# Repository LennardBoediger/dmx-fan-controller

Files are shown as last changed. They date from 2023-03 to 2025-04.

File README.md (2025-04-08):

# DMX Fan Controller
Speed controller for two old industrial fans.

https://user-images.githubusercontent.com/11893651/213900107-9a194785-94d3-4e1d-9f15-b6ec5db4715c.mov

<br>
The final installation will use two fans, a powerful fog machine and a stroboscope to create a neat effect.<br>

## Documentation 
The Fans are powerd by three-phase alternating current and come with an 0-10V control line. The lowest possible speed setting during runtime is 1.6V but 2.6V is required to start the motors from standstill

The controller board is based on the Arduino Nano (ATmega328).<br>
For the Fan Control line a 0-5V 10Bit DAC is used. The output voltage is then amplified, so that we end up with an 0-10V 10Bit DAC.<br>
To communicate over the DMX-Bus, the board is equipped with an MAX485E RS-485 transceiver.<br>
The DMX channel can be selected using a DIP switch.<br>
Additionally there is an manual control override, which allows the fan to be set to a constant speed.<br>
Mounting holes are M3.
#### Schematic:
Schematic-v2

## Safety instructions
Please don't die when using large spinning fan blades that are powered by three-phase current.

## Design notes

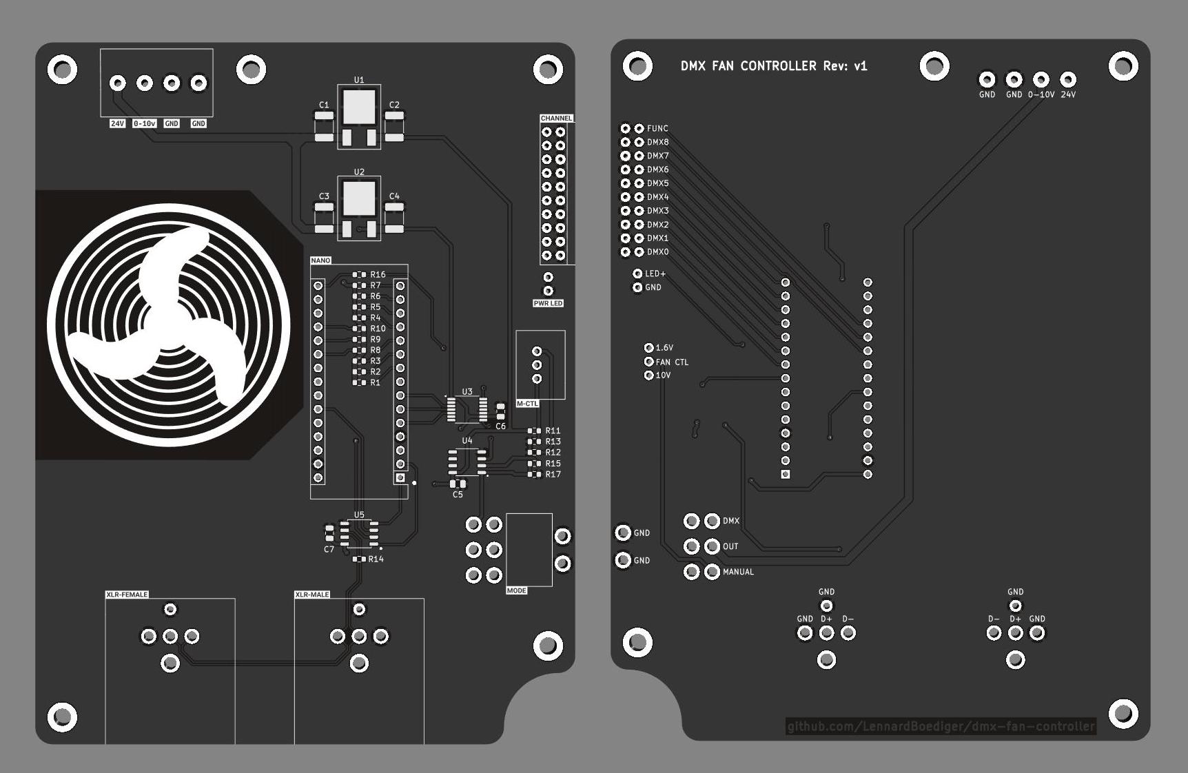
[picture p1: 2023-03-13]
.img/fan-controller-pcb-rendering.jpg

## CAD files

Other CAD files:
hardware/fan-controller-pcb/edge_cuts.FCStd

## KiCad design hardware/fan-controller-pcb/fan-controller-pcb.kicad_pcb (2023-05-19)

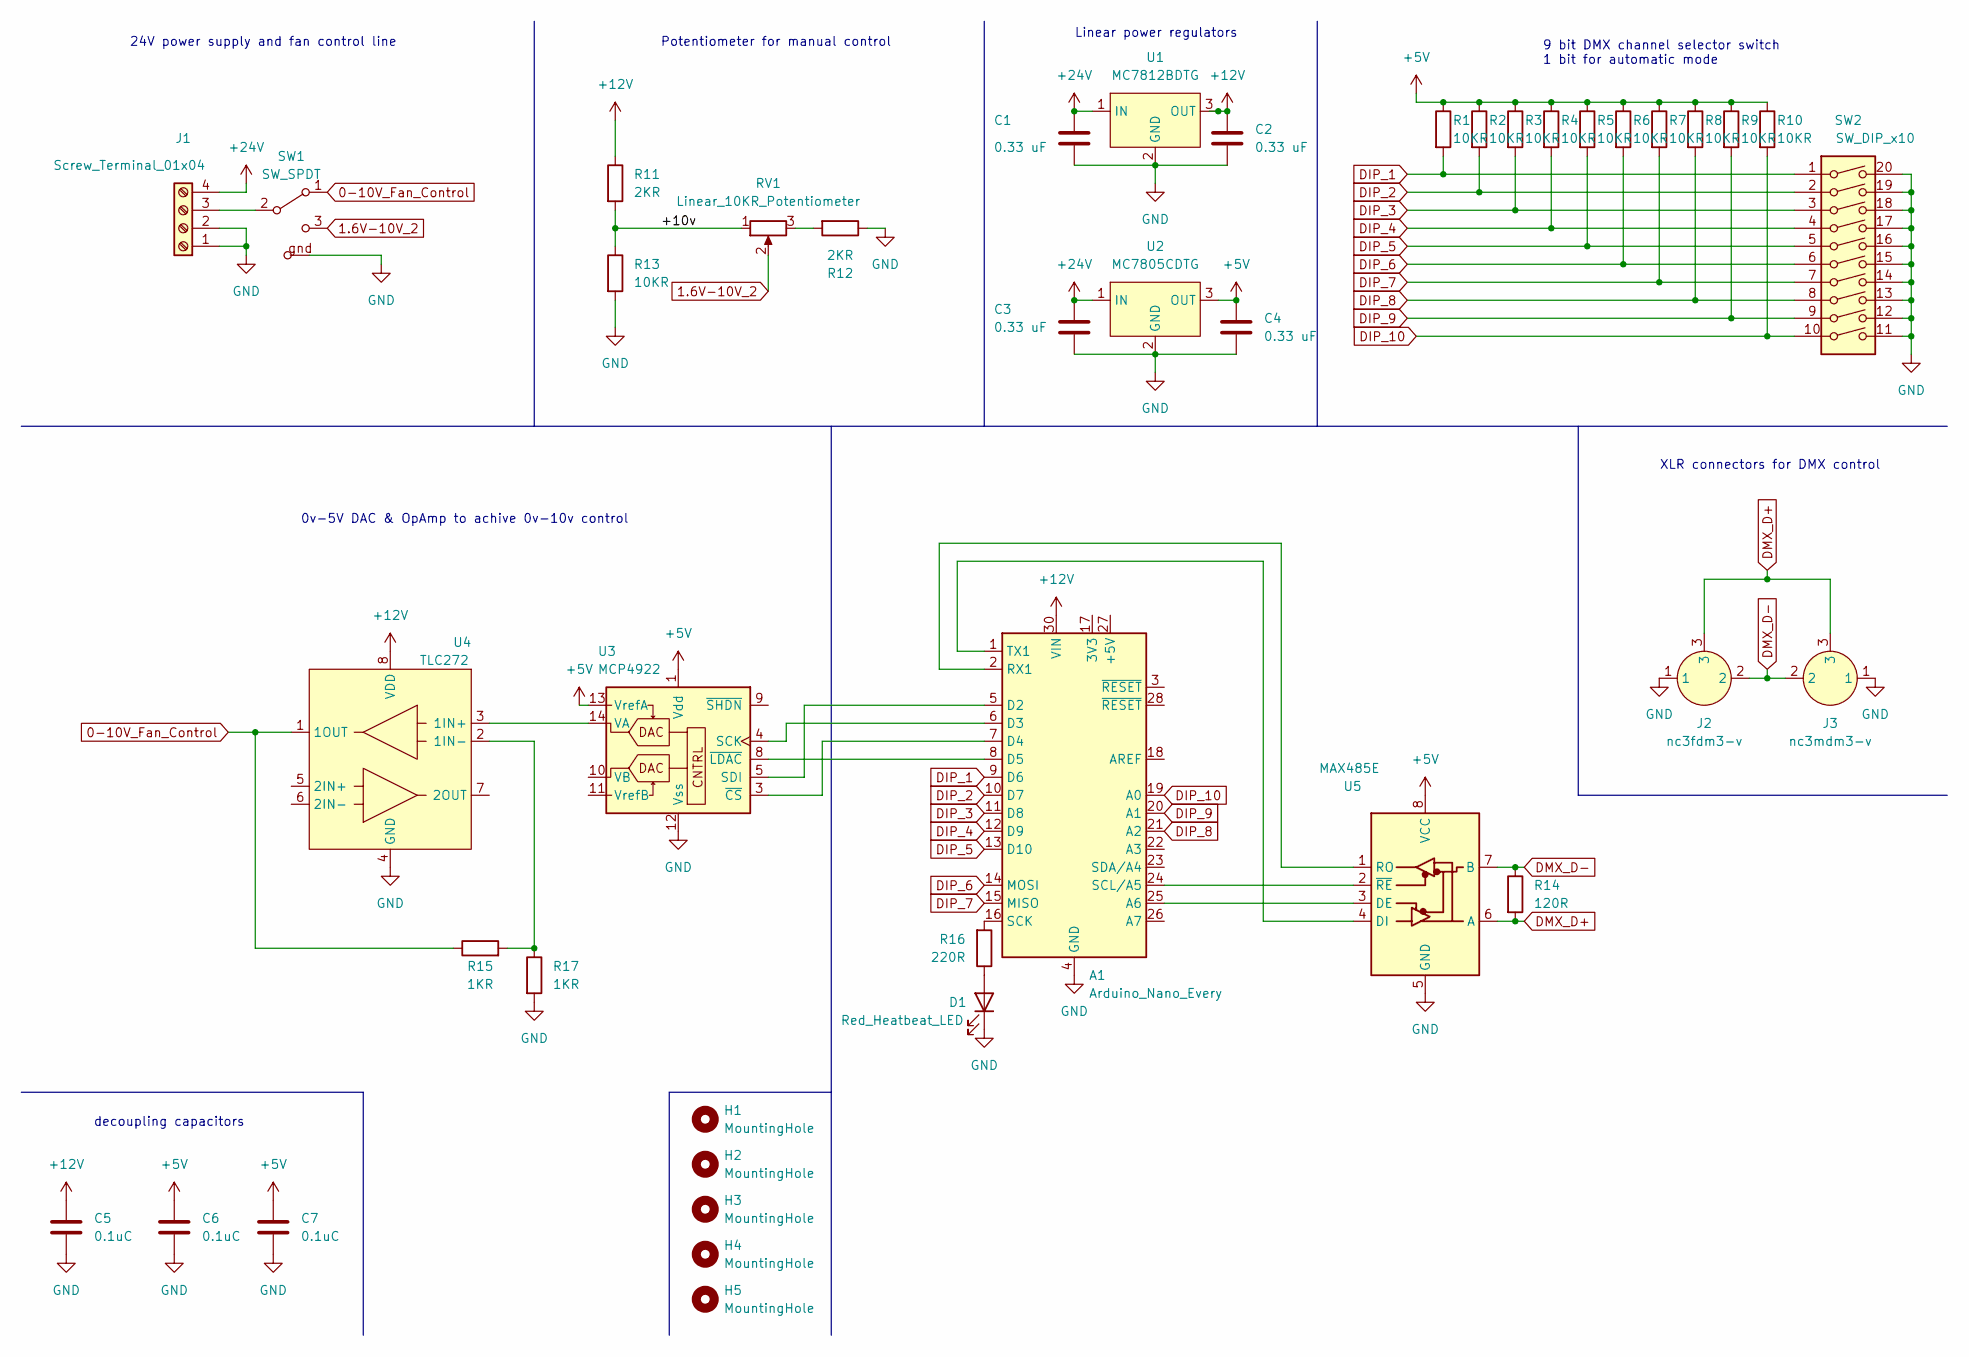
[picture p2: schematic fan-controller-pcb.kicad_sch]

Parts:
A1: Arduino_Nano_Every; Arduino_Nano
C1, C2, C3, C4: 0.33 uF; C_1812_4532Metric
C5, C6, C7: 0.1uC; C_0805_2012Metric
D1: Red_Heatbeat_LED; LED_D3.0mm_Horizontal_O1.27mm_Z6.0mm
H1, H2, H3, H4, H5: MountingHole; MountingHole_3.2mm_M3_ISO14580_Pad_TopBottom
J1: Screw_Terminal_01x04; TerminalBlock_Altech_AK300-4_P5.00mm
J2: nc3fdm3-v; nc3fdm3-h
J3: nc3mdm3-v; nc3mdm3-h
R1, R2, R3, R4, R5, R6, R7, R8, R9, R10, R13: 10KR; R_0603_1608Metric
R11, R12: 2KR; R_0603_1608Metric
R14: 120R; R_0603_1608Metric
R15, R17: 1KR; R_0603_1608Metric
R16: 220R; R_0603_1608Metric
RV1: Linear_10KR_Potentiometer; Potentiometer_Vishay_148-149_Single_Horizontal
SW1: SW_SPDT; WS-TOTV_6.35_Right_Angle_Toggle_Switch
SW2: SW_DIP_x10; WS-DITU_Compact_THT_Right_Angled
U1: MC7812BDTG
U2: MC7805CDTG; MC785BDTG
U3: MCP4922; MCP4912
U4: TLC272; tlc272a
U5: MAX485E

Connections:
0-10V_Fan_Control: R15.1, SW1.1 (A), U4.1 (1OUT)
1.6V-10V_2: RV1.2, SW1.3 (C)
+5V: C4.1, C6.1, C7.1, R1.1, R2.1, R3.1, R4.1, R5.1, R6.1, R7.1, R8.1, R9.1, R10.1, U2.3 (OUT), U3.1 (Vdd), U3.13 (VrefA), U5.8 (VCC)
+12V: A1.30 (VIN), C2.1, C5.1, R11.1, U1.3 (OUT), U4.8 (VDD)
+24V: C1.1, C3.1, J1.4, U1.1 (IN), U2.1 (IN)
/+10v: R11.2, R13.1, RV1.1
DIP_1: A1.9 (D6), R1.2, SW2.1
DIP_2: A1.10 (D7), R2.2, SW2.2
DIP_3: A1.11 (D8), R3.2, SW2.3
DIP_4: A1.12 (D9), R4.2, SW2.4
DIP_5: A1.13 (D10), R5.2, SW2.5
DIP_6: A1.14 (MOSI), R6.2, SW2.6
DIP_7: A1.15 (MISO), R7.2, SW2.7
DIP_8: A1.21 (A2), R8.2, SW2.8
DIP_9: A1.20 (A1), R9.2, SW2.9
DIP_10: A1.19 (A0), R10.2, SW2.10
DMX_D+: J2.3, J3.3, R14.2, U5.6 (A)
DMX_D-: J2.2, J3.2, R14.1, U5.7 (B)
GND: A1.4 (GND), A1.29 (GND), C1.2, C2.2, C3.2, C4.2, C5.2, C6.2, C7.2, D1.1 (K), J1.1, J1.2, J2.1, J3.1, R12.1, R13.2, R17.2, SW1.gnd (GND), SW2.11, SW2.12, SW2.13, SW2.14, SW2.15, SW2.16, SW2.17, SW2.18, SW2.19, SW2.20, U1.2 (GND), U2.2 (GND), U3.12 (Vss), U4.4 (GND), U5.5 (GND)
unnamed: A1.1 (TX1), U5.4 (DI)
unnamed: A1.2 (RX1), U5.1 (RO)
unnamed: A1.5 (D2), U3.5 (SDI)
unnamed: A1.6 (D3), U3.4 (SCK)
unnamed: A1.7 (D4), U3.3 (~CS)
unnamed: A1.16 (SCK), R16.2
unnamed: A1.24 (SCL/A5), U5.2 (~RE)
unnamed: A1.25 (A6), U5.3 (DE)
unnamed: D1.2 (A), R16.1
unnamed: J1.3, SW1.2 (B)
unnamed: R12.2, RV1.3
unnamed: R15.2, R17.1, U4.2 (1IN-)
unnamed: U3.14 (VA), U4.3 (1IN+)

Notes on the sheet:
24V power supply and fan control line
Potentiometer for manual control
0v-5V DAC & OpAmp to achive 0v-10v control
Linear power regulators
XLR connectors for DMX control
9 bit DMX channel selector switch 1 bit for automatic mode
decoupling capacitors

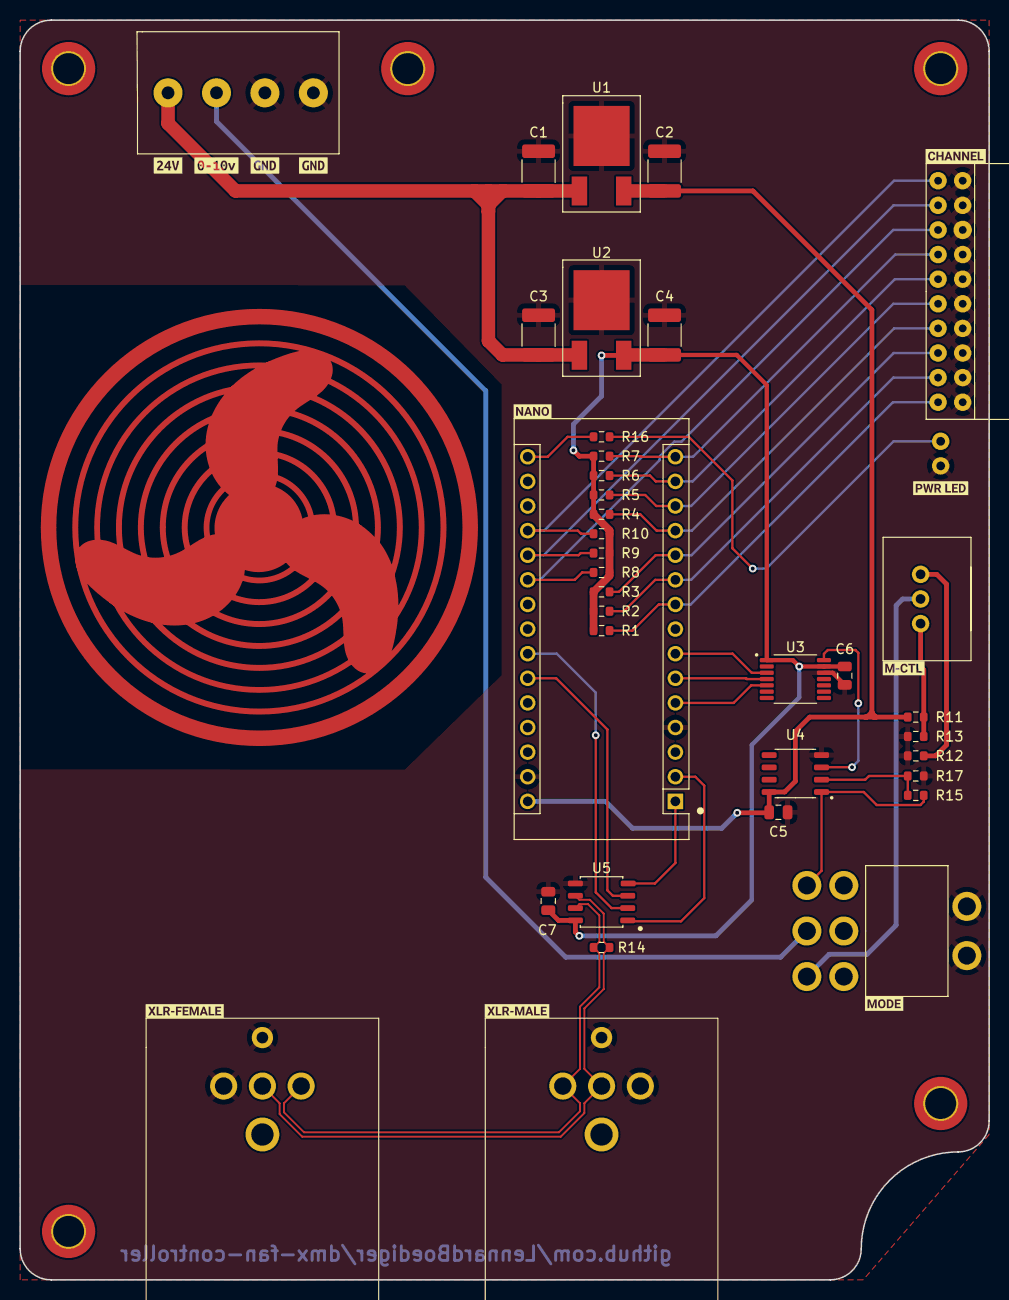
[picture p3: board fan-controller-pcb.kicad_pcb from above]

Board: 2 copper layers, 100.0 x 130.0 mm, 53 parts (0 on the bottom side), 32 nets.

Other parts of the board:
kibuzzard-63FA74A1: G***; kibuzzard-63FA74A1
kibuzzard-63FA74BB: G***; kibuzzard-63FA74BB
kibuzzard-63FA74F3: G***; kibuzzard-63FA74F3
kibuzzard-63FA7528: G***; kibuzzard-63FA7528
kibuzzard-640DCC4D: G***; kibuzzard-640DCC4D
kibuzzard-640DCC6D: G***; kibuzzard-640DCC6D
kibuzzard-640DCC52: G***; kibuzzard-640DCC52
kibuzzard-640DCC68: G***; kibuzzard-640DCC68
kibuzzard-640DCC72: G***; kibuzzard-640DCC72
kibuzzard-640DCC79: G***; kibuzzard-640DCC79
kibuzzard-640DCC82: G***; kibuzzard-640DCC82

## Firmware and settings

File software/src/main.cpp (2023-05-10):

#include <Arduino.h>
#include <DMXSerial.h>

#define DAC_MAX_VALUE 4095
#define DAC_MIN_VALUE 0
#define DMX_MAX_VALUE 255

// SPI Pins for DAC
const int CSPin = 4;
const int SCKPin = 3;
const int MOSIPin = 2;

// DIP switch pins for DMX address 
const int DMX0 = 6;
const int DMX1 = 7;
const int DMX2 = 8;
const int DMX3 = 9;
const int DMX4 = 10;
const int DMX5 = 11;
const int DMX6 = 12;
const int DMX7 = 16;
const int DMX8 = 15;
const int DMXfunc = 14;

// This function transmits data via SPI to the DAC (MCP4922)
// WRITE COMMAND REGISTER FOR MCP4922 (12-BIT DAC):
// Bit 15: channel (A=0, B=1), 
// Bit 14: Buffer (default=0), 
// Bit 13: Gain (1x=1, 2x=0), 
// Bit 12: shutdown (active=1. inactive-0),
// Bit 11-0: DAC Input Data bits.
// p. 24
void setDac(unsigned long value){ 
  unsigned long dacRegister = 0b0011000000000000;
  // Set channel A
  dacRegister &= ~(1 << 15);
  // Generate the two bytes that will be sent to the DAC
  unsigned long dacSendBytes = dacRegister | value;

  // Start SPI transmission
  digitalWrite(CSPin, LOW); 
  for(int i = 0; i < 16; i++){
    digitalWrite(MOSIPin, bitRead(dacSendBytes, 15-i));
    delay(2);
    digitalWrite(SCKPin, HIGH);
    delay(2);
    digitalWrite(SCKPin, LOW);
  }
  digitalWrite(CSPin, HIGH);
}

void setup() {
  // SPI
  pinMode(CSPin, OUTPUT);
  pinMode(SCKPin, OUTPUT);
  pinMode(MOSIPin, OUTPUT);
  digitalWrite(CSPin, HIGH);
  //DMX
  pinMode(DMX0, INPUT);
  pinMode(DMX1, INPUT);
  pinMode(DMX2, INPUT);
  pinMode(DMX3, INPUT);
  pinMode(DMX4, INPUT);
  pinMode(DMX5, INPUT);
  pinMode(DMX6, INPUT);
  pinMode(DMX7, INPUT);
  pinMode(DMX8, INPUT);
  DMXSerial.init(DMXReceiver);
}

void loop() {
  uint16_t DMXChannel = !digitalRead(DMX0) + (!digitalRead(DMX1) << 1) + (!digitalRead(DMX2) << 2) + (!digitalRead(DMX3) << 3) + (!digitalRead(DMX4) << 4) + (!digitalRead(DMX5) << 5) + (!digitalRead(DMX6) << 6)+ (!digitalRead(DMX7) << 7) + (!digitalRead(DMX8) << 8);
  setDac((DAC_MAX_VALUE / DMX_MAX_VALUE) * DMXSerial.read(DMXChannel));
  delay(4);
} 

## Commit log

2023-02-15 add pcb files
    [edge_cuts.FCStd, fan-controller-pcb.kicad_pcb, fan-controller-pcb.kicad_sch]
2023-02-22 avoid KiCad's messiness
2023-03-13 update PCB: edge cuts, routing, symbol_lib, footprint_lib, art & data sheets
    [edge_cuts.FCStd, fan-controller-pcb.kicad_pcb, fan-controller-pcb.kicad_sch]
2023-03-13 update PCB: add GND-plane & PCB Name
    [fan-controller-pcb.kicad_pcb]
2023-03-13 add schematic as pdf
2023-03-13 pcb rendering
2023-03-13 add Schematic as svg
2023-04-29 reorient F.Fab information
    [fan-controller-pcb.kicad_pcb]
2023-05-10 Fix the OP-Amp circuit
    [fan-controller-pcb.kicad_sch]
2023-05-10 Fix the MCP4922 footprint and adapting the traces
    [fan-controller-pcb.kicad_pcb]
2023-05-19 minor routing improvements and adding gerber files
    [fan-controller-pcb-B_Cu.gbr, fan-controller-pcb-B_Mask.gbr, fan-controller-pcb-B_Paste.gbr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]
2023-05-19 update schematic export
2023-05-19 update HW-Rev to v2
    [fan-controller-pcb-B_Cu.gbr, fan-controller-pcb-B_Mask.gbr, fan-controller-pcb-B_Paste.gbr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]
